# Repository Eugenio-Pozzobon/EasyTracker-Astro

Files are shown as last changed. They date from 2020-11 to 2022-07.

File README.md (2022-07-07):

# Desenvolvimento de uma Plataforma Equatorial de Baixo Custo para Astrofotografia

Este repositório armazena os arquivos desenvolvidos durante o Trabalho de Conclusão de Curso do Aluno Eugênio Pozzobon, sob orientação do professor Rafael Beltrame.
O TCC pode ser obtido neste link: https://repositorio.ufsm.br/handle/1/25238

## Aplicativo Android
* Os arquivos do  _software_ Android, que opera junto com a eletrônica arquivada neste repositório, pode ser encontrado [neste link.](https://github.com/Eugenio-Pozzobon/EasyTracker-Android-App)
* Para apenas instalar, acesse [este link para a Google Play](https://play.google.com/store/apps/details?id=com.epp.com.easytracker) 

## Licença
Os arquivos de documentação estão licenciados sob Creative Commons CC BY-SA. Dessa forma, são livre para redistribuição. Códigos do Hardware Embarcado estão licenciados sob GPLV3, implicando que os autores devem ser permanentemente creditados por esses arquivos. Os arquivos de desenvolvimento CAD são livres.

### Como contribuir?
Antes de qualquer coisa, leia e estude a documentação do TCC. Após isso, envie um email para eugenio.pozzobon@acad.ufsm.br para saber como ajudar no projeto.

---

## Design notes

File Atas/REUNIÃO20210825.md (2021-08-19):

### Algoritmo de calibração de bússola de um DJI (?)

* Auto detecta erro de calibração
	* Verifica quando as constantes de calibração (valores mínimos e máximos de medição não estão conferindo com a realidade)
* Auto detecta calibração concluída
	* Giroscópio

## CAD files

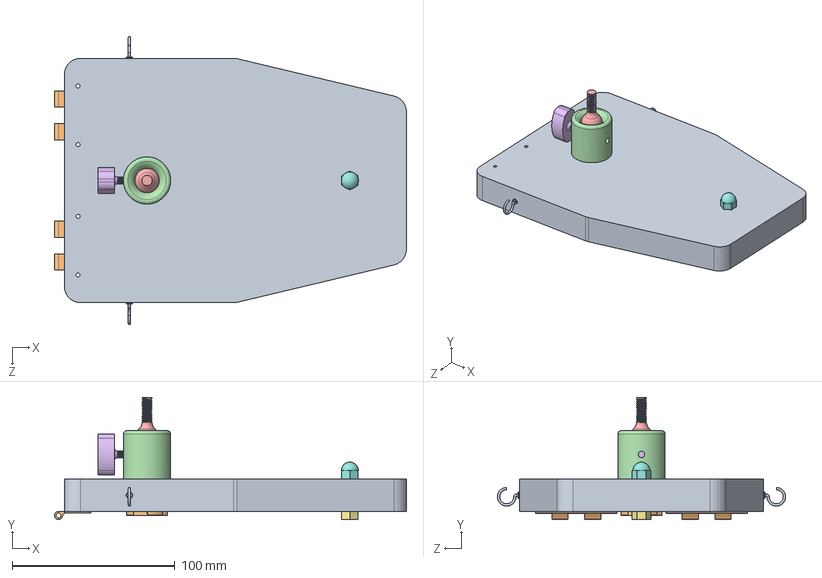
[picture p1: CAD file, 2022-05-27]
CAD/Base Superior/BDT_S_A_17_v01.SLDASM
216.0 x 75.0 x 176.9 mm
BDT_S_P_13_v01
BDT_S_P_15_v01 x 2
BDT_G_P_22_v01
BDT_S_P_18_v01
BDT_S_P_19_v01
BDT_S_P_20_v01
BDT_G_F_25_v01
BDT_G_F_26_v01
BDT_G_F_24_v01 x 2
TNUT-3-8

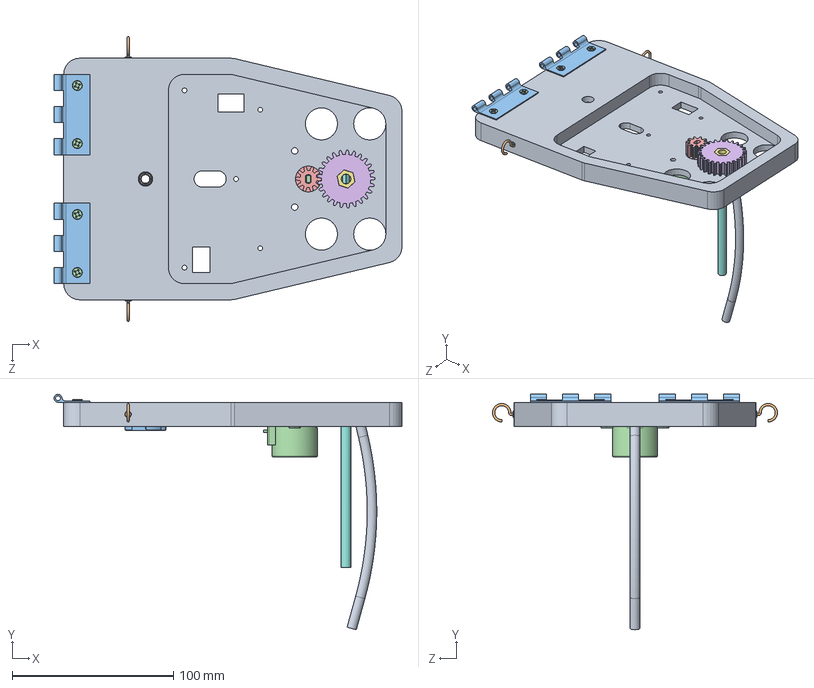
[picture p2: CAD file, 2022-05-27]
CAD/Base Inferior/BDT_I_A_16_v01.SLDASM
216.0 x 146.2 x 176.9 mm
BDT_I_P_11_v01
BDT_I_P_12_v01 x 2
BDT_E_P_01_v01
BDT_I_P_06_v01
BDT_I_P_07_v01
BDT_G_F_26_v01
Gambi^BDT_I_A_16_v01
BDT_G_F_05_v01
BDT_G_F_24_v01 x 2
flat countersunk head tapping screw_am x 4
INSERTO

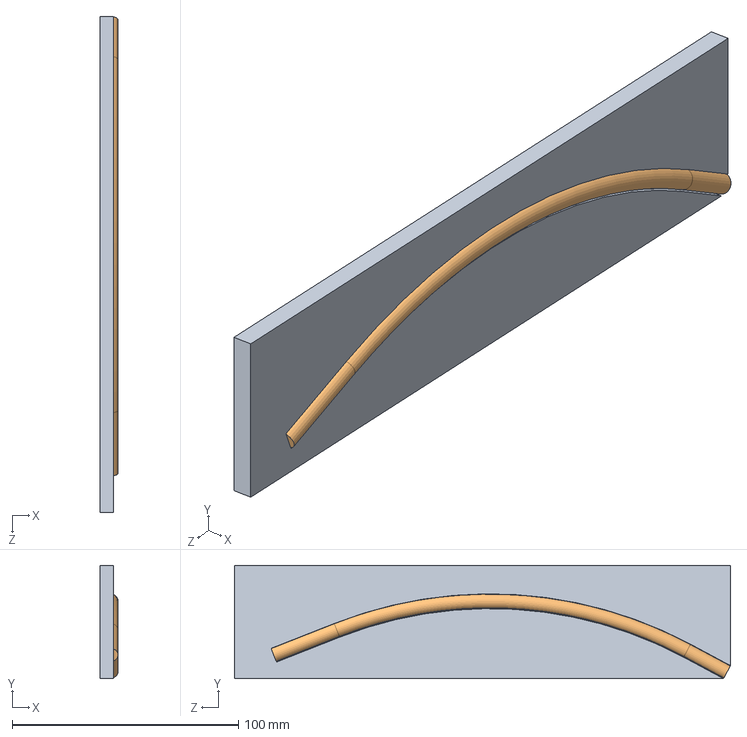
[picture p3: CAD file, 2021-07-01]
CAD/Fabricação/Montagem Gabarito.SLDASM
8.00 x 50.0 x 219.0 mm
Gabarito Eixo Curvo
BDT_G_F_05_v01

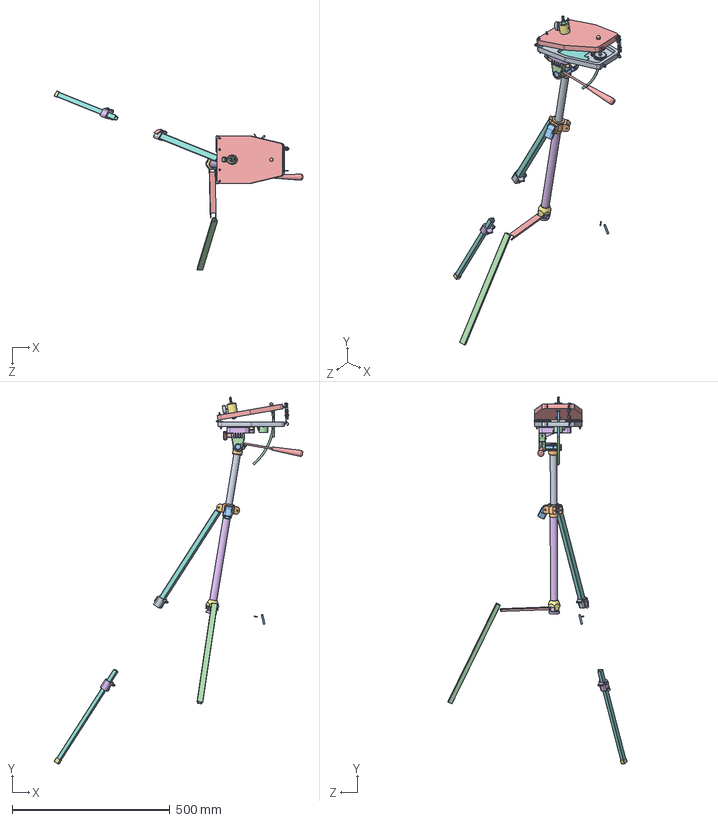
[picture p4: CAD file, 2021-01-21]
CAD/BDT_GLOBAL_ASSEMBLY.SLDASM
787.4 x 1162.0 x 567.4 mm
BDT_I_P_11_v01
BDT_G_P_22_v01 x 2
BDT_I_P_12_v01 x 2
Step - 28BYJ-48
hex nut style 1_am x 8
flat head screw_am x 8
BDT_G_F_24_v01 x 4
BDT_I_P_06_v01
BDT_I_P_07_v01
PORCAM6tTRAVA x 2
BDT_G_F_05_v01
BDT_S_P_13_v01
BDT_S_P_15_v01 x 2
BDT_S_P_18_v01
BDT_S_P_19_v01
BDT_S_P_20_v01
socket button head cap screw_ai
PORCAM6
BDT_G_P_14_v01 x 2
BDT_G_F_10_v01 x 2
PCBfake^BDT_GLOBAL_ASSEMBLY

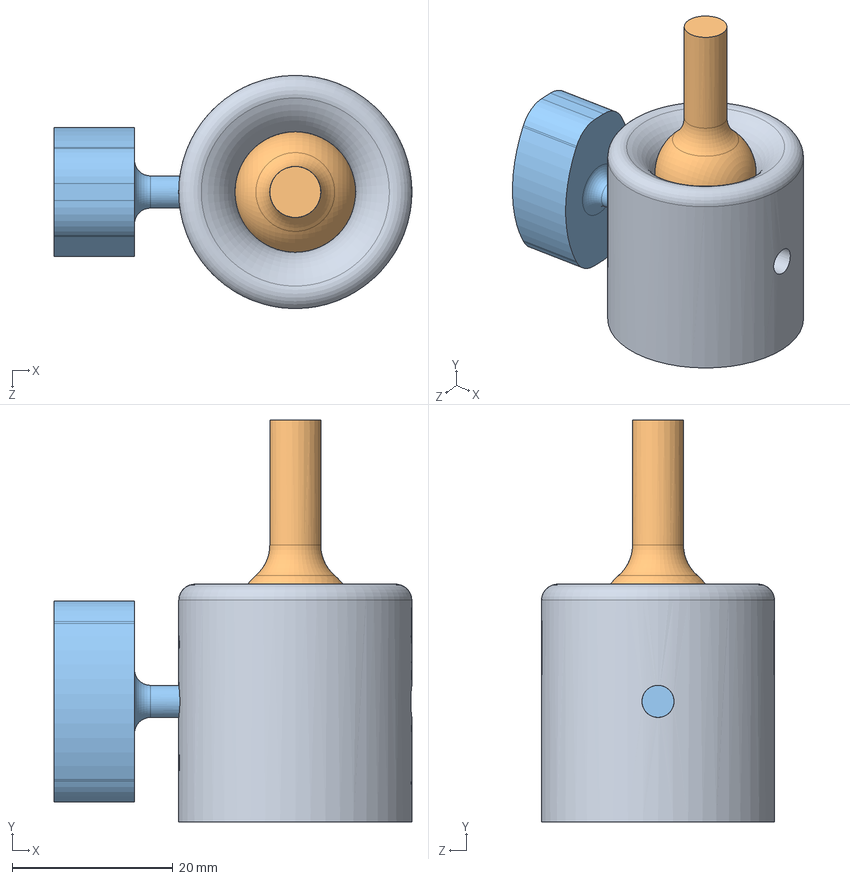
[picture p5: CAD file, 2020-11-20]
CAD/Base Superior/Cabeça de Tripé/BDT_S_A_21_v01.SLDASM
44.5 x 50.0 x 29.0 mm
BDT_S_P_18_v01
BDT_S_P_19_v01
BDT_S_P_20_v01

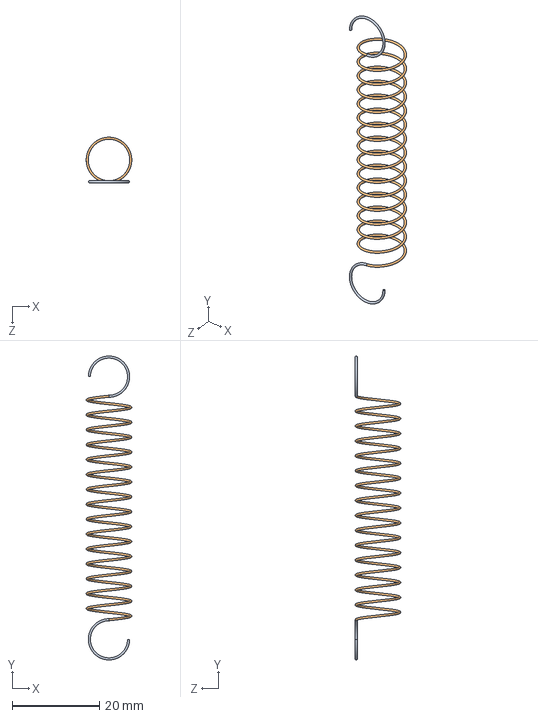
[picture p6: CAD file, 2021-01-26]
CAD/Fixadores/Mola de Tração.sldasm
10.5 x 69.9 x 10.5 mm
BDT_G_F_10_v01 x 2
BDT_G_F_09_v01

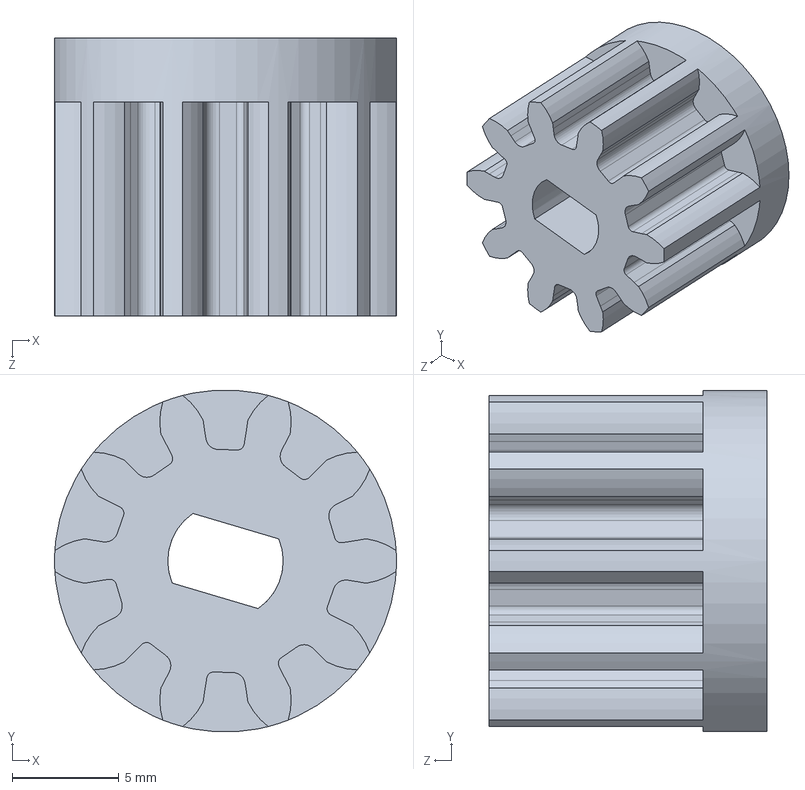
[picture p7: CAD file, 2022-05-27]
CAD/Base Inferior/BDT_I_P_06_v01.sldprt
16.0 x 16.0 x 13.0 mm

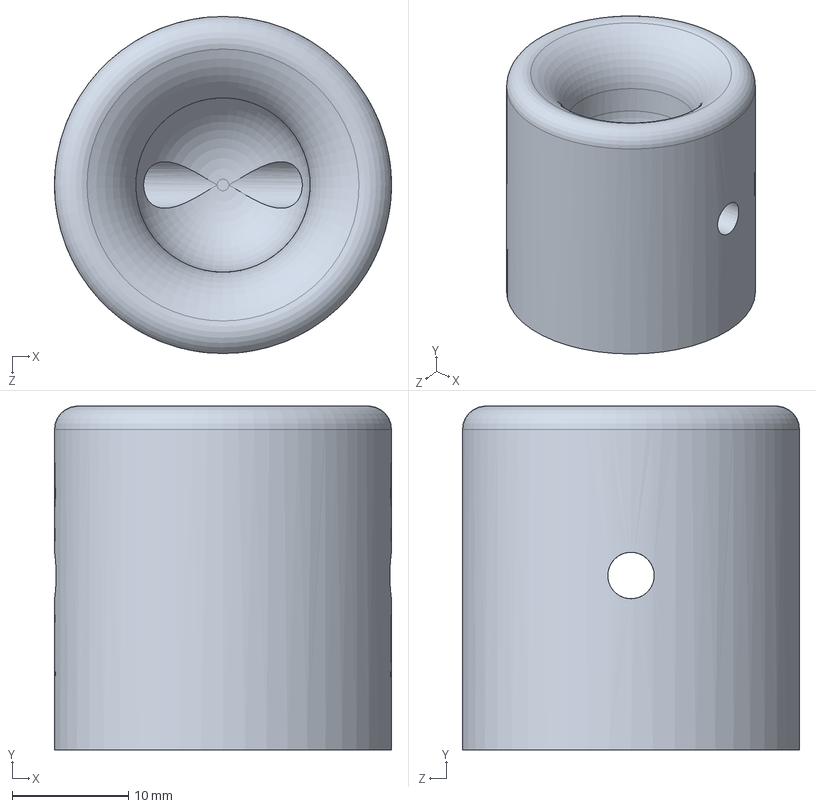
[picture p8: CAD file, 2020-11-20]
CAD/Base Superior/Cabeça de Tripé/BDT_S_P_18_v01.SLDPRT
29.0 x 29.6 x 29.0 mm

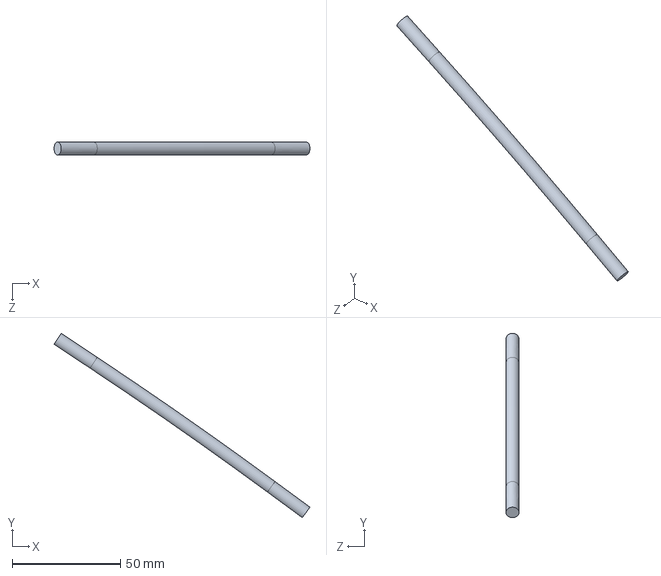
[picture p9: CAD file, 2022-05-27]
CAD/BDT_G_F_05_v01.sldprt
118.2 x 85.1 x 6.00 mm

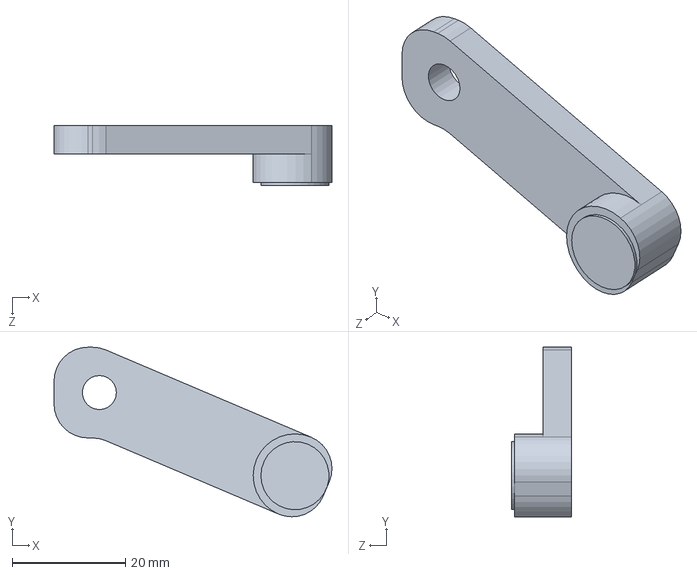
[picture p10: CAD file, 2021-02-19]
CAD/Eletrônica/BDT_E_P_03_v01.SLDPRT
49.0 x 29.9 x 10.5 mm

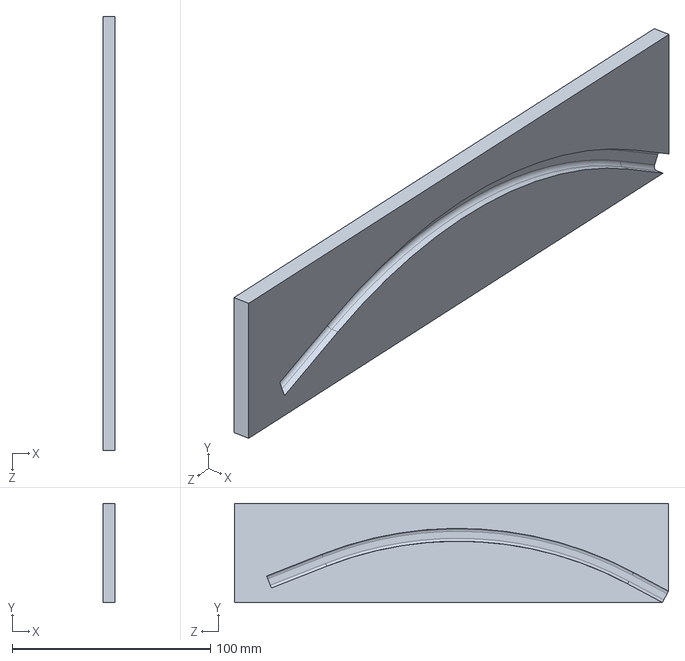
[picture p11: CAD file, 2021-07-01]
CAD/Fabricação/Gabarito Eixo Curvo.SLDPRT
6.00 x 50.0 x 219.0 mm

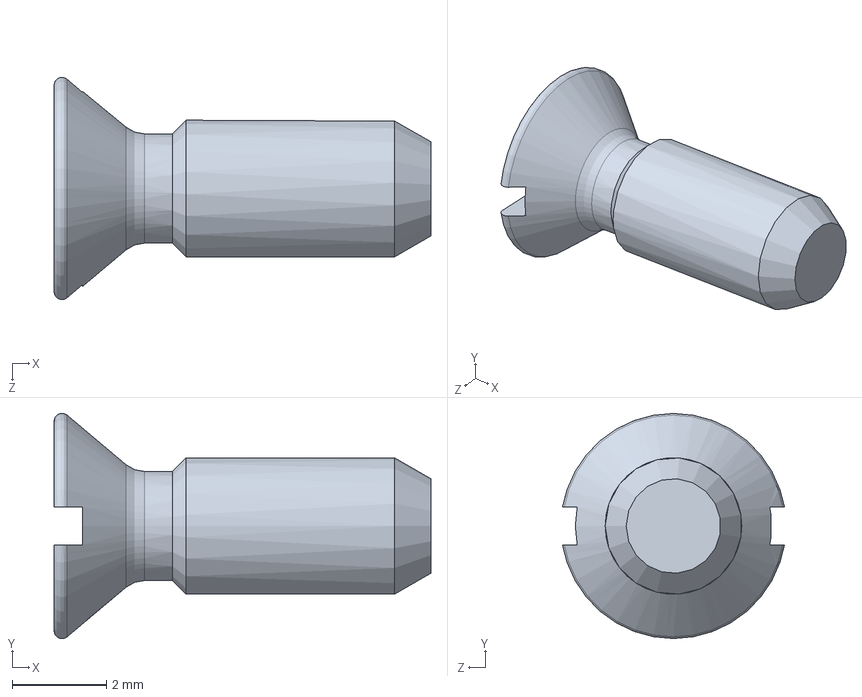
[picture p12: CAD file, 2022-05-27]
CAD/Fixadores/a.SLDPRT
8.00 x 4.78 x 4.72 mm

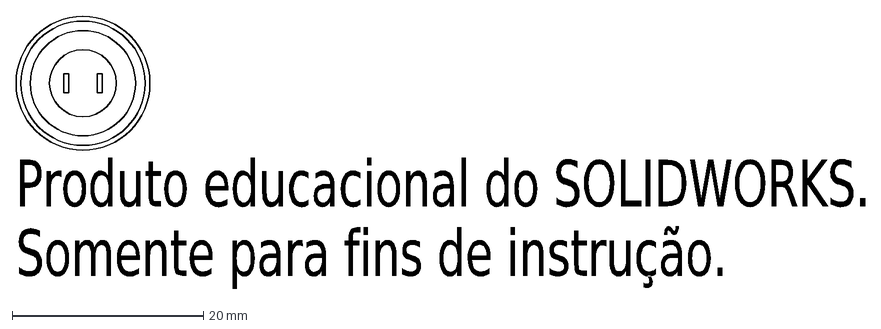
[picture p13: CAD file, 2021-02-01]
Electronics/button.DXF
Produto educacional do SOLIDWORKS.
Somente para fins de instrução.

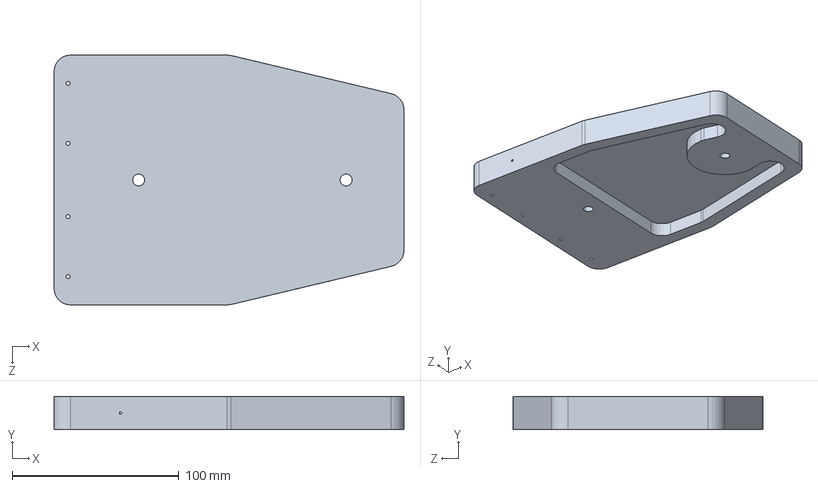
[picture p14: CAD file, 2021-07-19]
CAD/Base Superior/BDT_S_P_13_v01.SLDPRT
210.0 x 20.0 x 150.0 mm

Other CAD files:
CAD/Base Superior/Cabeça de Tripé/BDT_S_P_19_v01.SLDPRT
CAD/BDT_G_P_14_v01.sldprt
CAD/Eletrônica/BDT_E_P_27_v01.SLDPRT
CAD/Fixadores/TNUT-3-8.SLDPRT
CAD/Base Inferior/BDT_I_P_07_v01.SLDDRW
CAD/Base Inferior/BDT_I_P_07_v01.sldprt
CAD/Base Inferior/BDT_I_P_11_v01.DXF
CAD/Base Inferior/BDT_I_P_11_v01.SLDPRT
CAD/Base Inferior/BDT_I_P_12_v01.SLDPRT
CAD/Base Inferior/INSERTO.SLDPRT
CAD/Base Superior/BDT_S_P_15_v01.SLDPRT
CAD/Base Superior/Cabeça de Tripé/BDT_S_P_20_v01.SLDPRT
CAD/Eletrônica/BDT_E_P_01_v01.SLDPRT
CAD/Eletrônica/BDT_E_P_02_v01.SLDPRT
CAD/Eletrônica/BDT_E_P_28_v01.SLDPRT
CAD/Eletrônica/BDT_E_P_29_v01.SLDPRT
CAD/Eletrônica/Peça1.SLDPRT
CAD/Eletrônica/startbutton.SLDPRT
CAD/Fabricação/BDT_E_P_03_v01.DWG
CAD/Fabricação/BDT_G_F_05_v01.SLDDRW
CAD/Fabricação/BDT_I_P_06_v01.STEP
CAD/Fabricação/BDT_I_P_07_v01.STEP
CAD/Fabricação/BDT_I_P_11_v01.DWG
CAD/Fabricação/BDT_I_P_11_v01.SLDDRW
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

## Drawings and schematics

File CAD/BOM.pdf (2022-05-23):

# BILL OF MATERIALS (BOM)

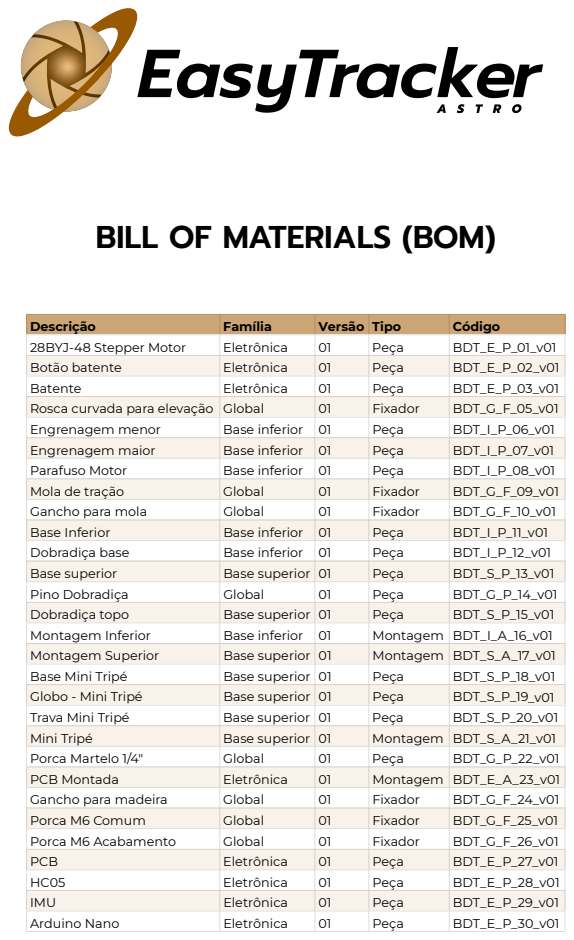
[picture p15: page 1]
Descrição; Família; Versão Tipo; Código; 28BYJ-48 Stepper Motor; Eletrônica; Peça; BDT_E_P_01_v01; Botão batente; BDT_E_P_02_v01; Batente; BDT_E_P_03_v01; Rosca curvada para elevação Global; Fixador; BDT_G_F_05_v01; Engrenagem menor; Base inferior 01; BDT_I_P_06_v01; Engrenagem maior; BDT_I_P_07_v01; Parafuso Motor; BDT_I_P_08_v01; Mola de tração; Global; BDT_G_F_09_v01; Gancho para mola; BDT_G_F_10_v01; Base Inferior; BDT_I_P_11_v01; Dobradiça base; BDT_I_P_12_v01; Base superior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

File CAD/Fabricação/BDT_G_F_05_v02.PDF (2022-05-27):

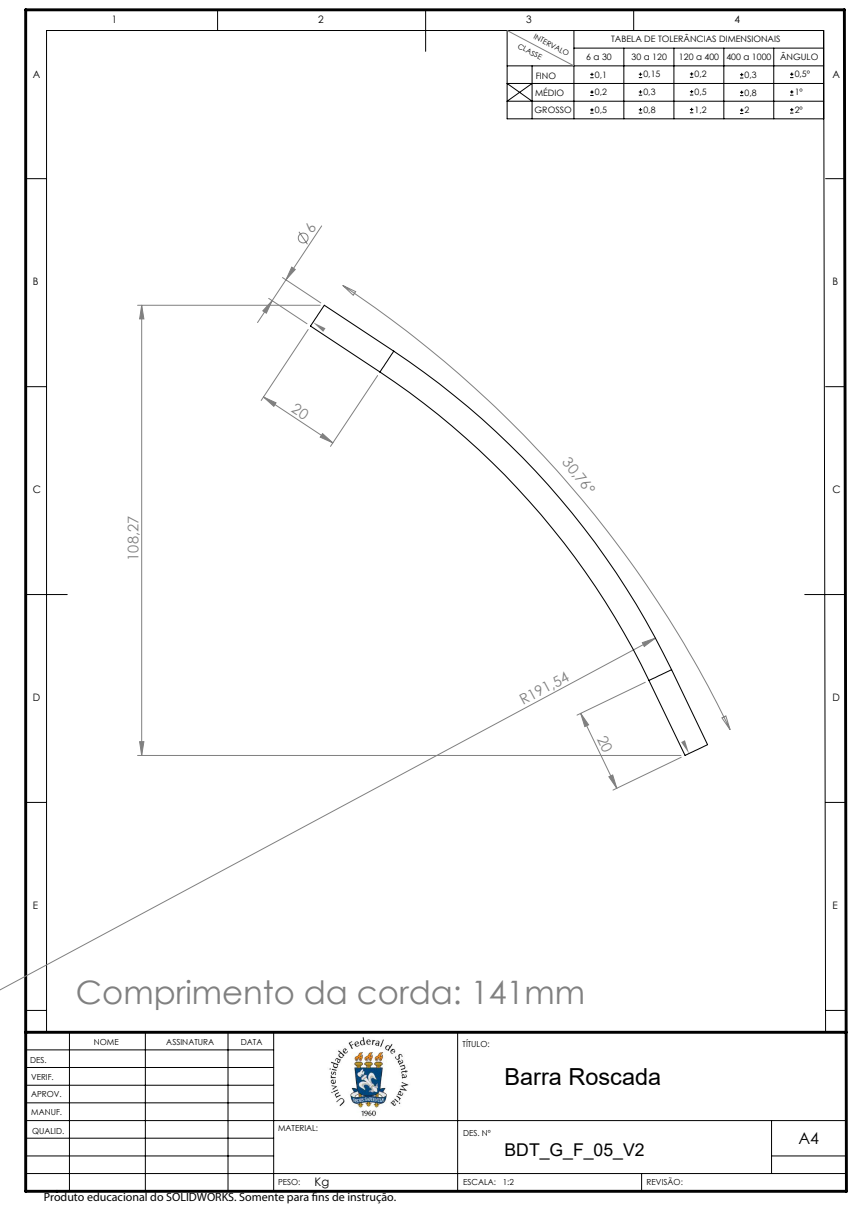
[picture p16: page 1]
ÂNGULO; TABELA DE TOLERÂNCIAS DIMENSIONAIS; ESCALA: 1:2; DES. Nº; Barra Roscada

Comprimento da corda: 141mm

Produto educacional do SOLIDWORKS. Somente para ns de instrução.

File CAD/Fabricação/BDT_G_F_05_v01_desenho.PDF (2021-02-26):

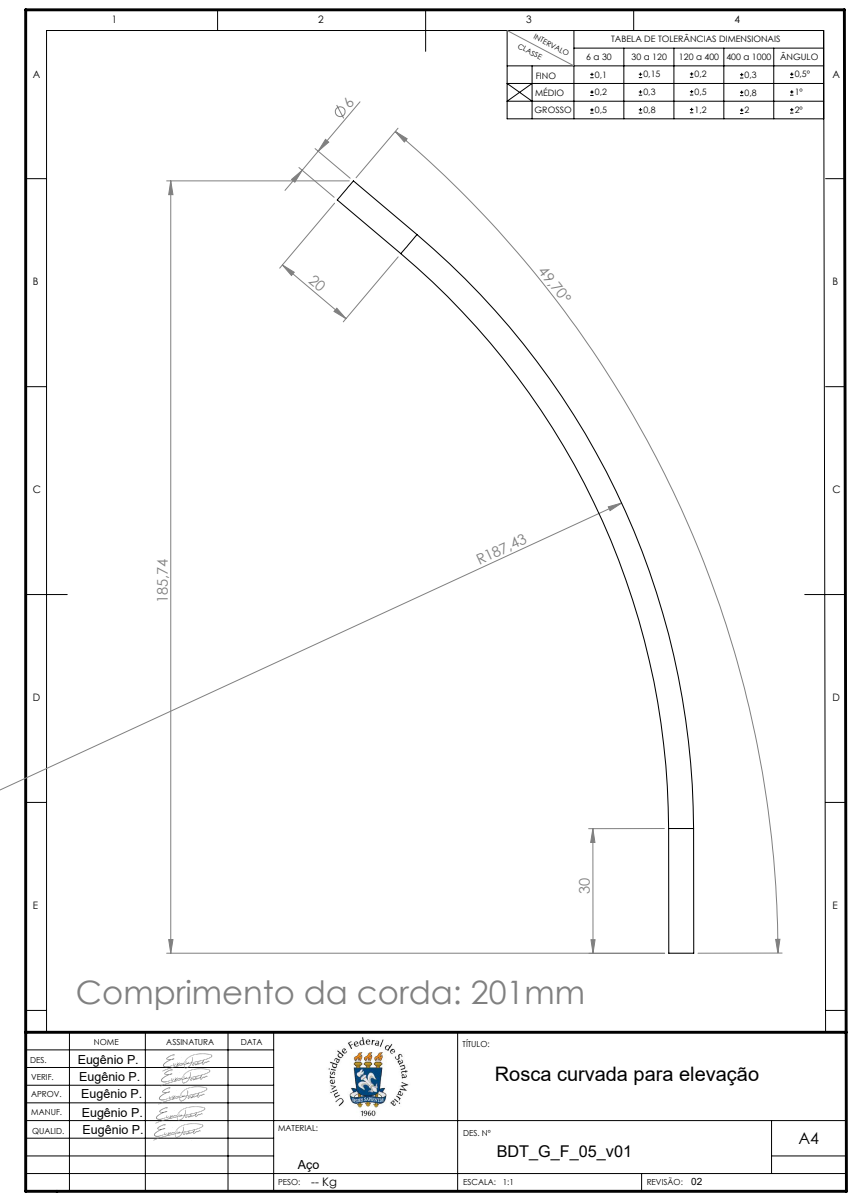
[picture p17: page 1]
ÂNGULO; TABELA DE TOLERÂNCIAS DIMENSIONAIS; ESCALA: 1:1; DES. Nº; REVISÃO:; Eugênio P. Eugênio P. Eugênio P.; Eugênio P.

Comprimento da corda: 201mm

TÍTULO:
Rosca curvada para elevação

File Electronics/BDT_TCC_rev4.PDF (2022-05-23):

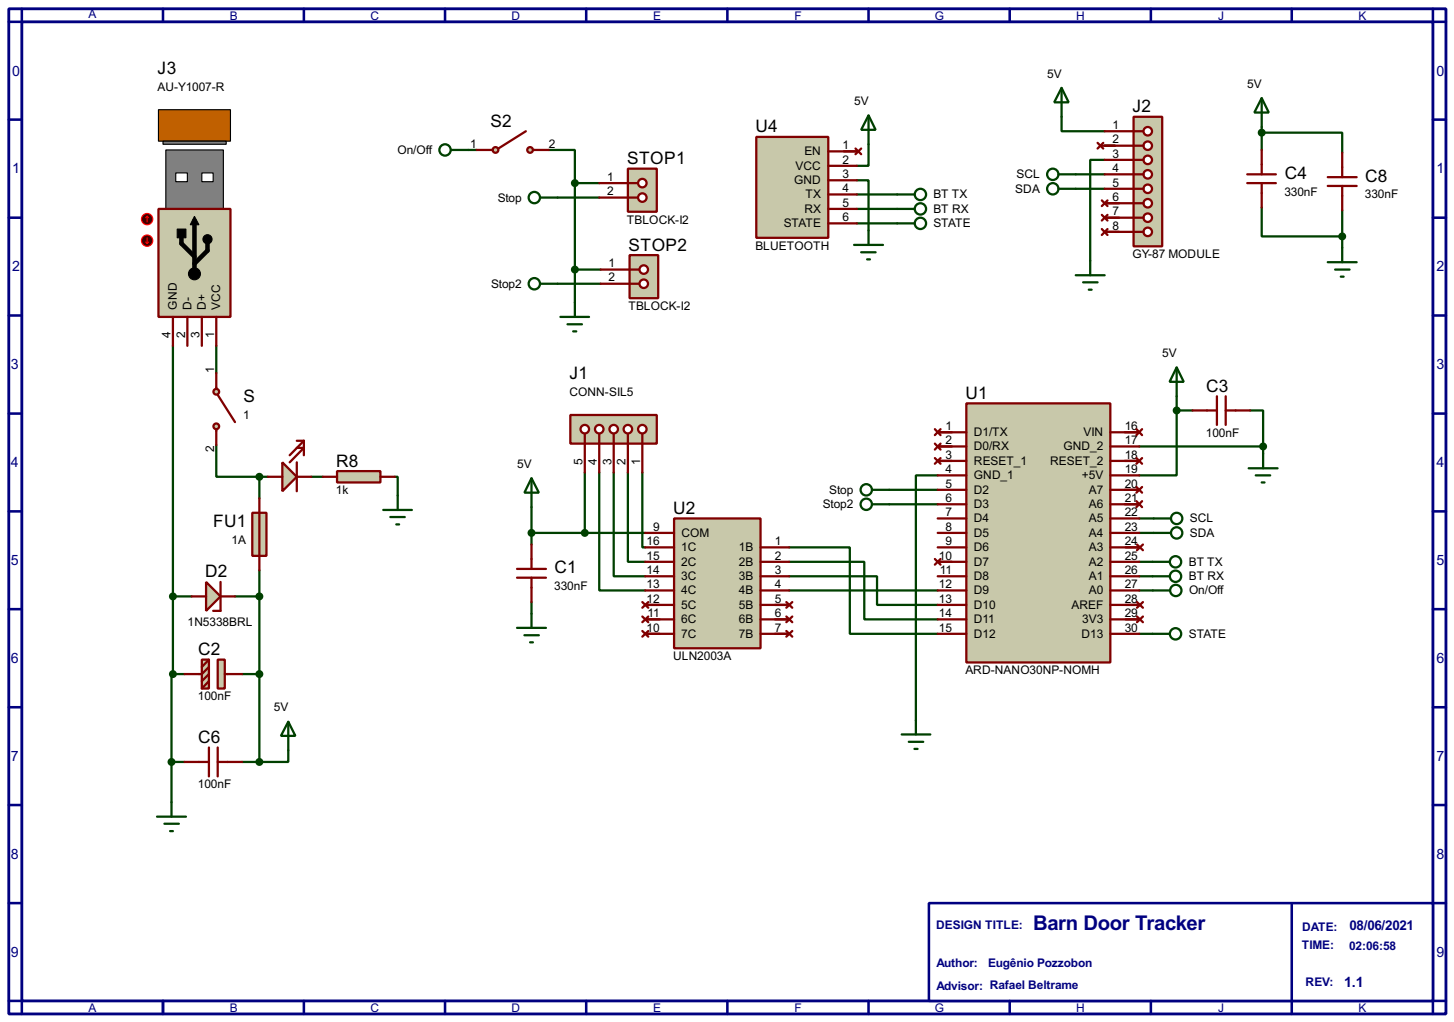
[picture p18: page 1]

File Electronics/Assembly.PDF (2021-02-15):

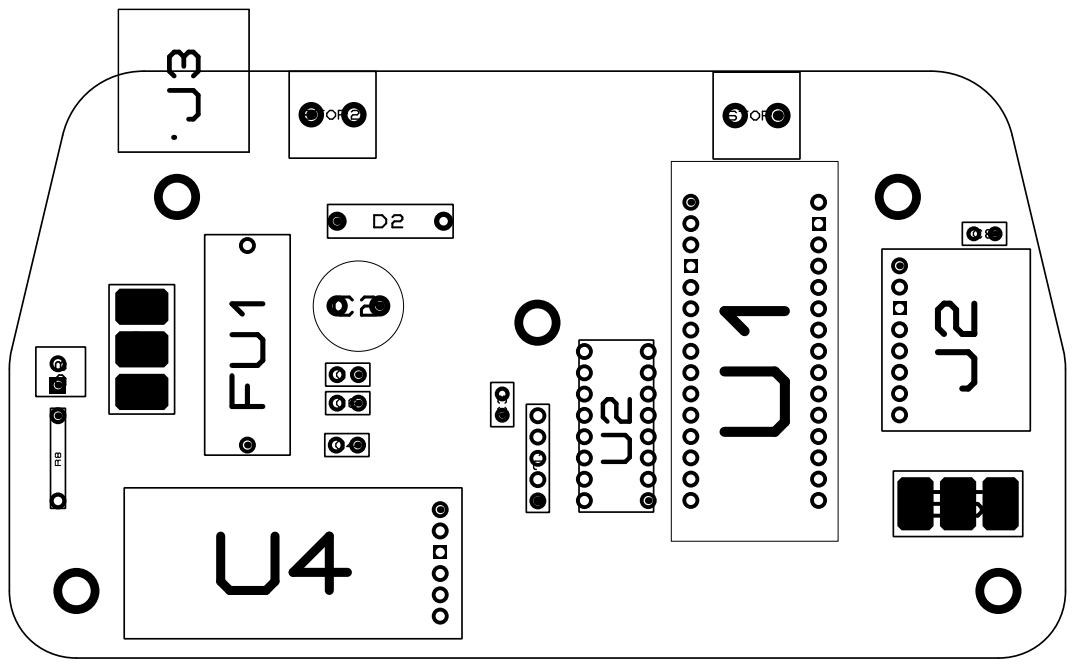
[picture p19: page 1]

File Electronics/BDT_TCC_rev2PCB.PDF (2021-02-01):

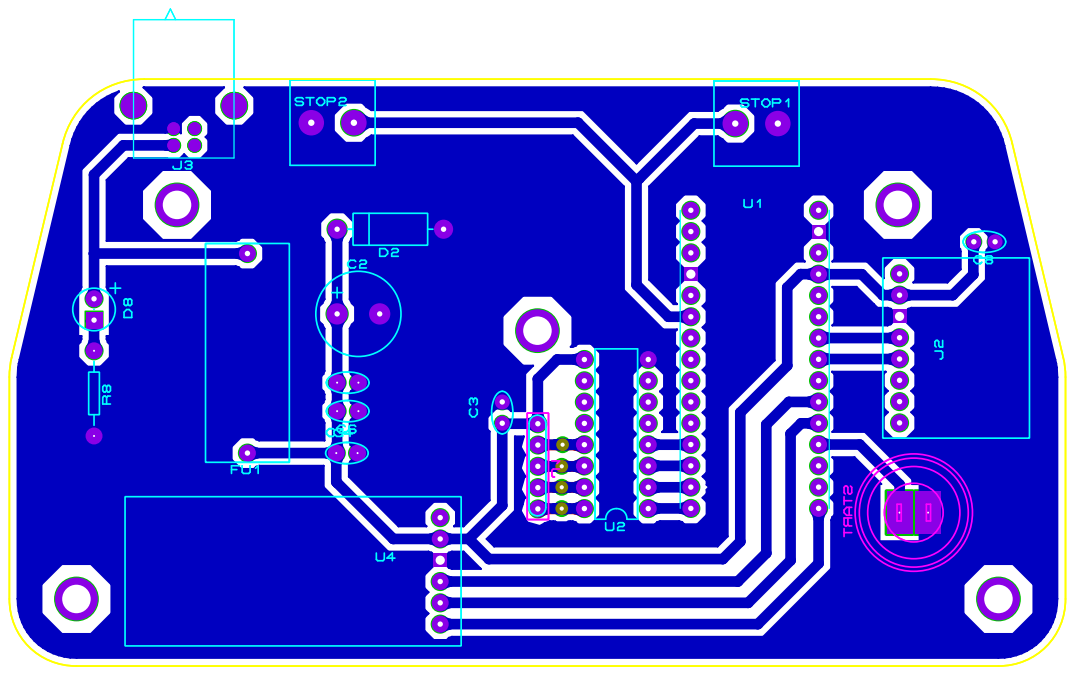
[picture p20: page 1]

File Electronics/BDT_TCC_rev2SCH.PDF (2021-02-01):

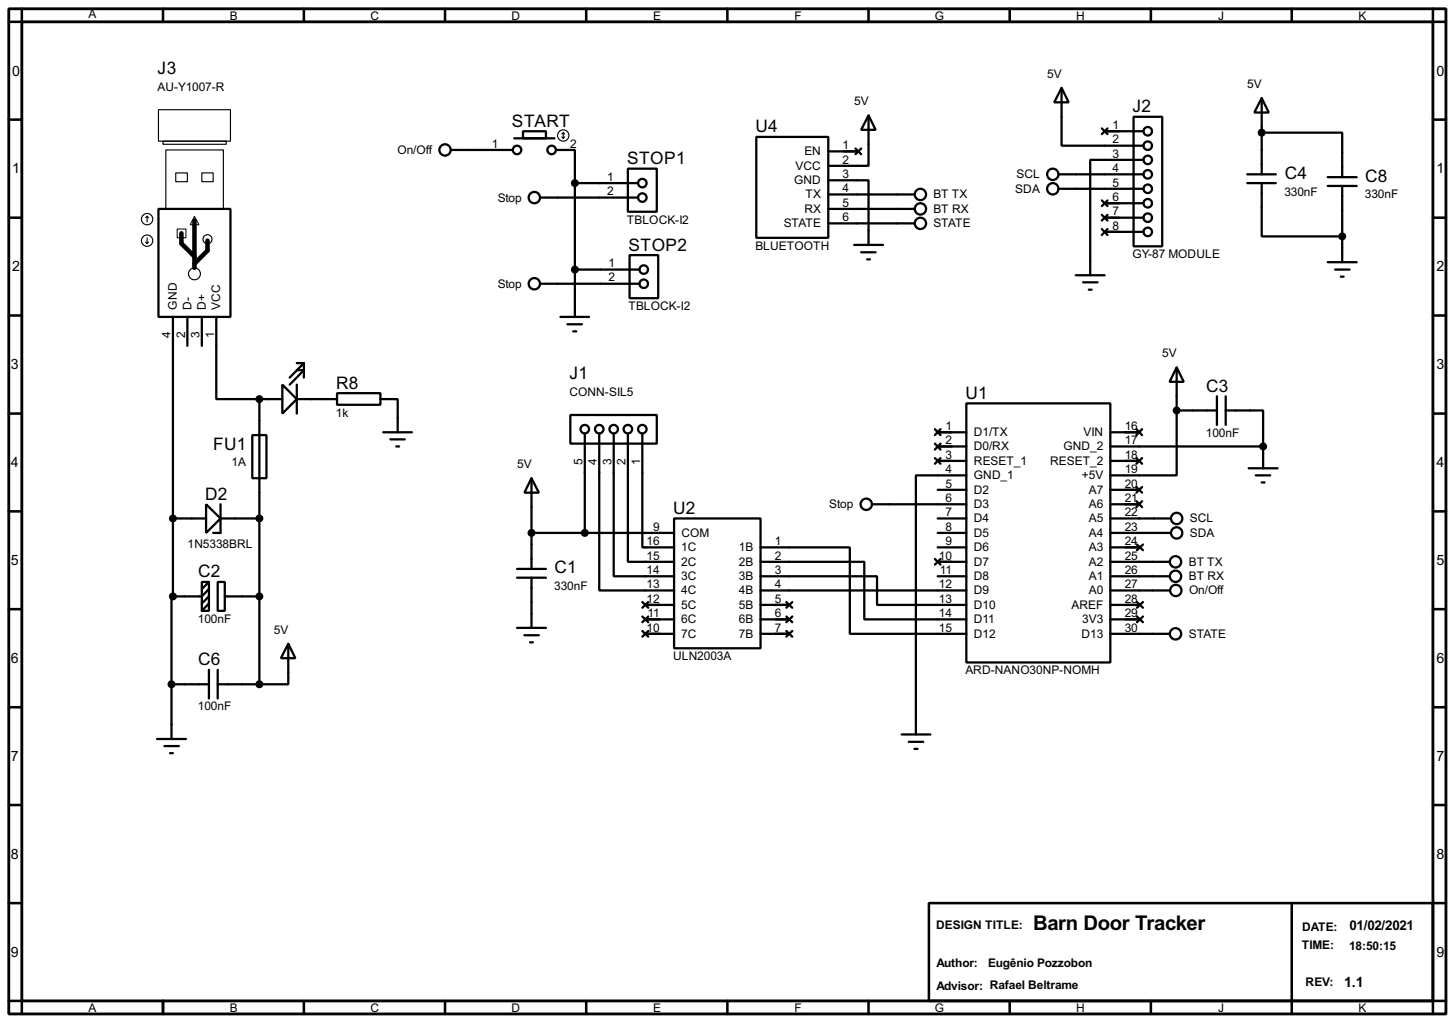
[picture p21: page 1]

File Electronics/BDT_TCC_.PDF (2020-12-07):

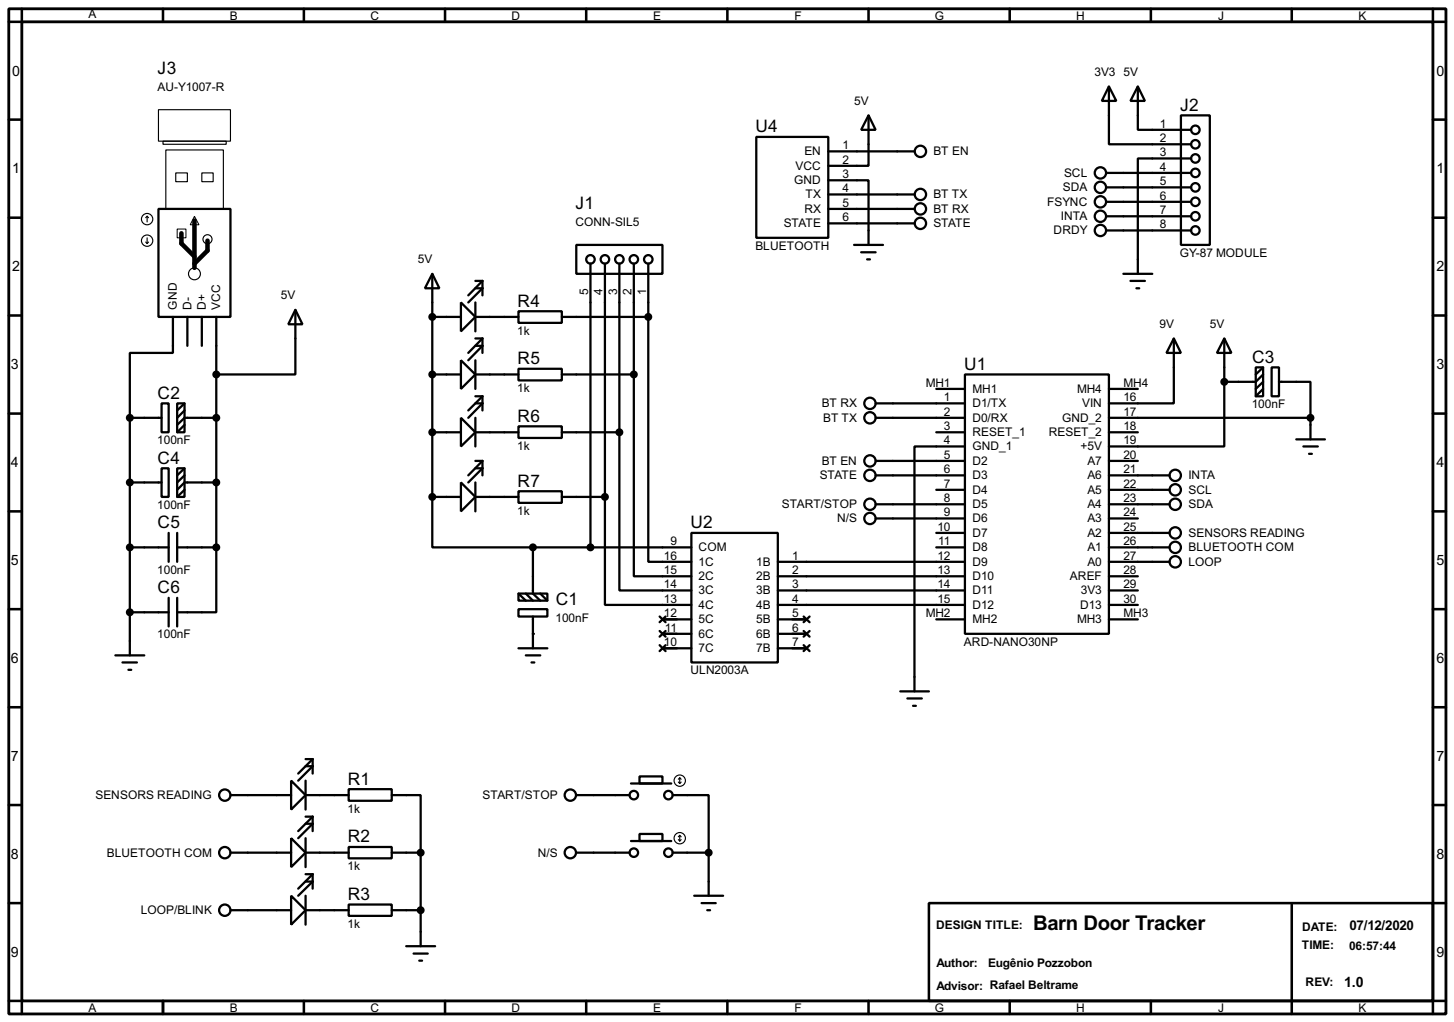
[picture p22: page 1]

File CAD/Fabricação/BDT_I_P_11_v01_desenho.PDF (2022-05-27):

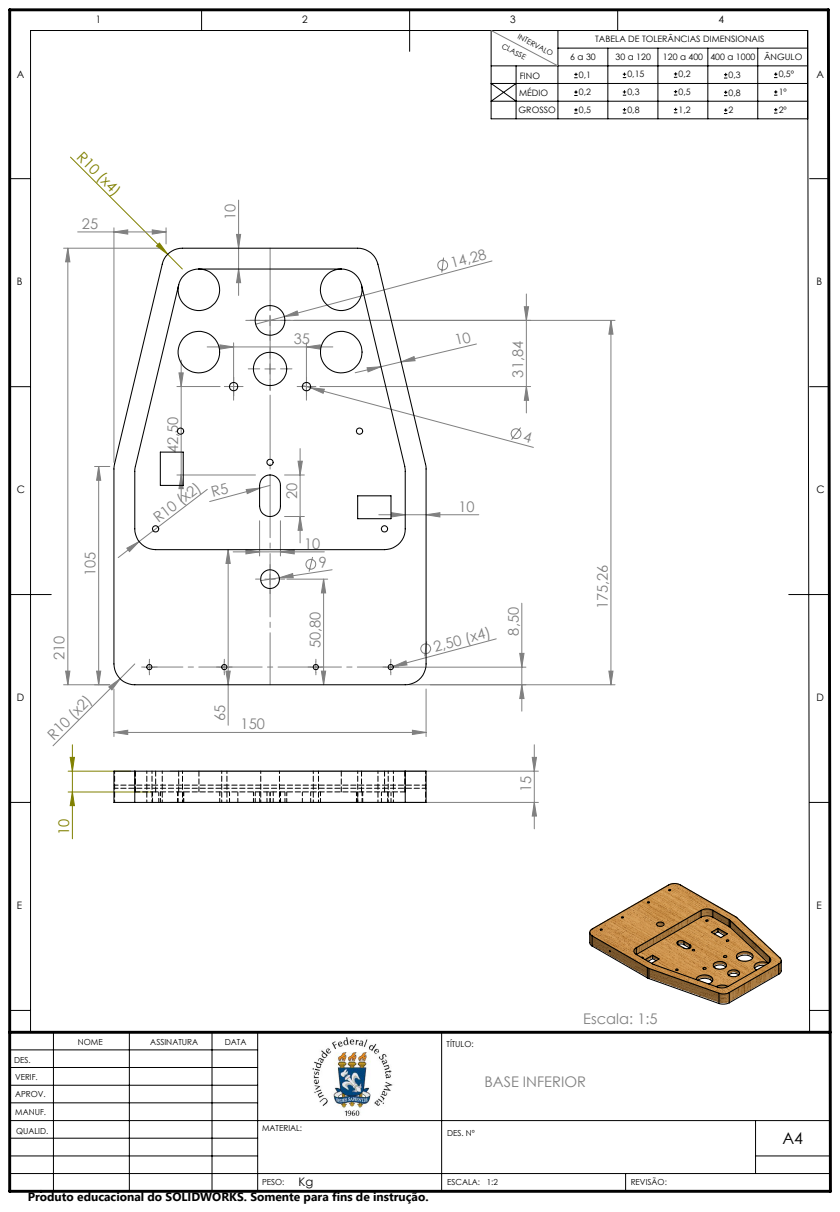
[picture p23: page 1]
ÂNGULO; TABELA DE TOLERÂNCIAS DIMENSIONAIS; Escala: 1:5; BASE INFERIOR; ESCALA: 1:2; DES. Nº

Produto educacional do SOLIDWORKS. Somente para fins de instrução.

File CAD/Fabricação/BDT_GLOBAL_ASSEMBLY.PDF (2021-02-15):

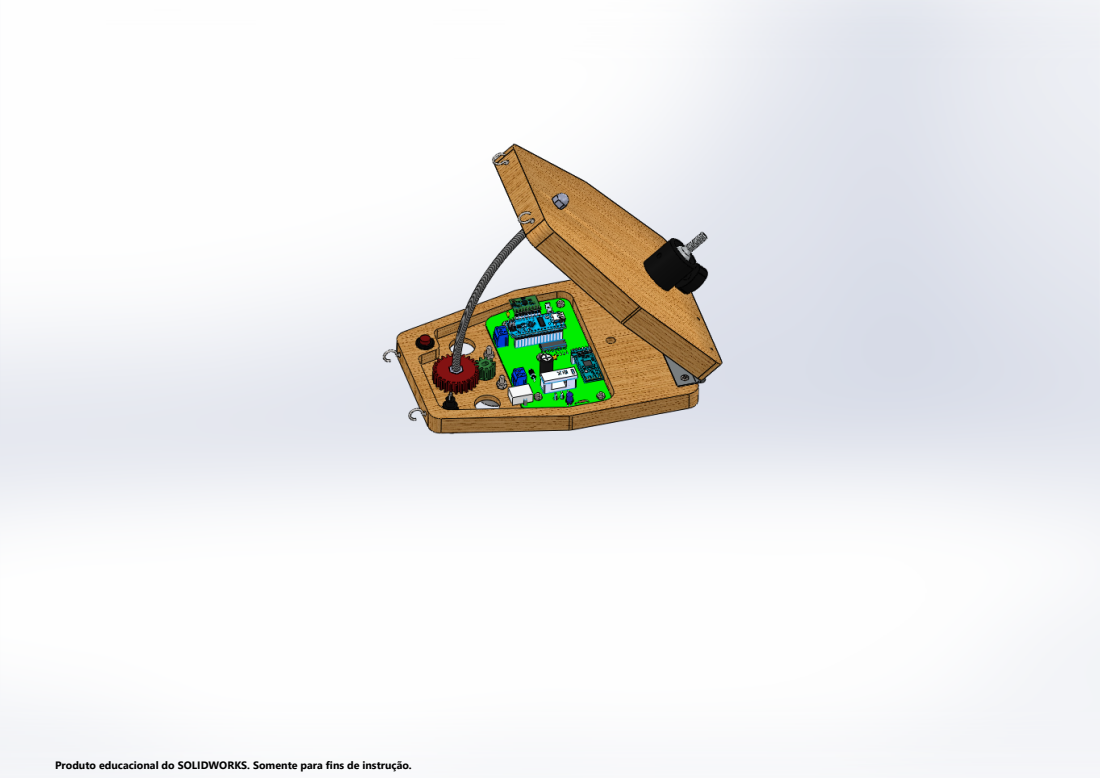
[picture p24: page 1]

Produto educacional do SOLIDWORKS. Somente para fins de instrução.

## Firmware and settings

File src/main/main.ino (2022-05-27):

/*
main.ino - main file of EasyTracker Astro System

Version: 1.0.0
Copyright (C) 2022  Eugênio Pozzobon

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
You should have received a copy of the GNU General Public License
along with this program.  If not, see <http://www.gnu.org/licenses/>.
*/

#include "configuration.h"

// Librarys includes
#include "Wire.h"
#include "MPU6050_bdt.h"
#include "HMC5883L_bdt.h"
#include "stp.h"
//#include <Stepper.h>

#include <SoftwareSerial.h>
#include <EEPROM.h>
#include <avr/wdt.h>

// Bluetooth variables
SoftwareSerial bluetoothSerial(16, 15); // RX/TX
unsigned long timerBluetoothRestartMessages = 0;
unsigned long timerBluetoothRecieveMessages = 0;
unsigned long timerBluetoothSendMessages = 0;
const byte bluetoothStatePin = 13;

//User Input Variables
char availableUserOption = '0';
bool manualDeactivation = true, remoteDeactivation = false;
bool manualActivation = false, lastManualActivation = false;
bool remoteActivation = false;

// Acelerometer variables
MPU6050 accelgyro;
float angleX, angleY, angleZ;
unsigned long gyroIntegrateTimer = 0; //Timer to interate Gyroscope axis and get Gyro part of Pitch and Roll angle.
const float accelGyroRelation = 0.5; //How mucth Gyro and Accel is consider for interate Pitch and Roll. 0 means that only accel will be used.

// Magnetometer variables
HMC5883L mag;
int mx, my, mz;
float mxCalibrated, myCalibrated, mzCalibrated;

// Calibration factors
int mxMin = EEPROM.read(0) << 8 | EEPROM.read(1);
int myMin = EEPROM.read(2) << 8 | EEPROM.read(3);
int mzMin = EEPROM.read(4) << 8 | EEPROM.read(5);
int mxMax = EEPROM.read(6) << 8 | EEPROM.read(7);
int myMax = EEPROM.read(8) << 8 | EEPROM.read(9);
int mzMax = EEPROM.read(10) << 8 | EEPROM.read(11);

// Calculation variables
const byte mediaMovelArray = 8;
float compassAngle = 0;
float reads[mediaMovelArray];

// Timer variables
unsigned long timerMpuData, timerStepperMicros = 0, timerLoop = 0;

// Stepper variables
boolean stepperState = false;
const int startButtonPin = 14;
const int stopButtonPin = 2;
const int stopButtonPin_sec = 3;
const int stepsPerRevolution = 4096 / 2;
HalfStepper myStepper = HalfStepper(stepsPerRevolution, 12, 10, 11, 9);

void setup() {
  //Initializate Whatchdog
  wdt_enable(WDTO_8S);

  // Initializate Variables
  for (int i = 0; i < mediaMovelArray; i++) {
    reads[i] = 0;
  }

  // Initializate Serial
#ifdef DEBUG
  Serial.begin(115200);
  printCalibrationInfo();
#endif

  // Initializate Bluetooth
  bluetoothSart();

  // Initializate I2C Bus
  beginI2cBus();
  initializeDevicesI2c();

  // Initializate Arduino pins
  //  pinMode(ledPin, OUTPUT);
  pinMode(startButtonPin, INPUT_PULLUP);
  pinMode(stopButtonPin, INPUT_PULLUP);
  pinMode(stopButtonPin_sec, INPUT_PULLUP);

  // Setup Stepper
  myStepper.setSpeed(STP_SPEED);
}

void loop() {

  wdt_reset();

  stepperState = checkStepperCondition();
  if (stepperState == true) {
    myStepper.step(runningSteps); //runs Stepper motor and elevate the plataform
    if (bluetoothSerial.available() > 0) {
      if (manualActivation && !remoteActivation) {
        bluetoothSerial.print("s,s\n");
      }
      availableUserOption = bluetoothSerial.read(); //flush buffer
    }
  } else {
    if (bluetoothSerial.available() > 0) {
      if (remoteActivation) {
        bluetoothSerial.print("n,n\n");
        remoteActivation = false;
      }
    }
  }

  if (stepperState == false) {
    getData();
    serialCommunication();
    bluetoothCommunication();
  }

  manageUserOption();

#ifdef DEBUG
//  Serial.print("manualActivation "); Serial.println(manualActivation);
//  Serial.print("manualDeactivation "); Serial.println(manualDeactivation);
//  Serial.print("remoteActivation "); Serial.println(remoteActivation);
//  Serial.print("remoteDeactivation "); Serial.println(remoteDeactivation); Serial.println();
#endif
}


bool checkStepperCondition() {
  int nullvar = analogRead(startButtonPin); //não tem função nenhuma, não serve pra nada, porém o código só funciona se estiver aqui!
  if (millis() > 5000) {// dont get the starting set of pullup as a true value
    if (!manualActivation && !digitalRead(startButtonPin)) {
      manualActivation = true;
      manualDeactivation = false;
      remoteDeactivation = false;
    }
    if (manualActivation && digitalRead(startButtonPin)) {
      manualActivation = false;
      manualDeactivation = true;
      remoteActivation = false;
    }
  }
  bool stopState = false;//(!digitalRead(stopButtonPin) || !digitalRead(stopButtonPin_sec));
  if(stopState){
    manualActivation = false;
    remoteActivation = false;
  }
  return ((manualActivation || remoteActivation) && (!manualDeactivation && !remoteDeactivation && !stopState));
}

bool checkBluetoothCondition() {
  return (!digitalRead(bluetoothStatePin));
}

void serialCommunication() {
#ifdef DEBUG
  while (Serial.available() > 0) {
    availableUserOption = Serial.read();
  }
#endif
}


/*
   @brief
   @note
   @param
   @return
*/
void manageUserOption() {
  if (availableUserOption == 'c') {
    compassCalibration();
  }
  if (availableUserOption == 's') {
    remoteActivation = true;
    remoteDeactivation = false;
    manualDeactivation = false;
    bluetoothSerial.print("s,s\n"); //while writebuffer isnt clean in android, send the buffer that trigger an internal clean
  }
  if (availableUserOption == 'n') {
    remoteDeactivation = true;
    remoteActivation = false;
    bluetoothSerial.print("n,n\n"); //while writebuffer isnt clean in android, send the buffer that trigger an internal clean
  }
  if (availableUserOption == 'r') {
    ressetCalibration();
  }
  if (availableUserOption == '1') {
    remoteActivation = true;
    remoteDeactivation = false;
  }
  availableUserOption = '0';
}

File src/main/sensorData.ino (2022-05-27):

/*
sensorData.ino - file that process sensor data at EasyTracker

Version: 1.0.0
Copyright (C) 2022  Eugênio Pozzobon

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
You should have received a copy of the GNU General Public License
along with this program.  If not, see <http://www.gnu.org/licenses/>.
*/

void getData() {
  if (((millis() - timerMpuData) >= 0) && !stepperState) {

    timerMpuData = millis();
    //1ms to get all data with 400kHz and 5ms with 100kHz
    accelgyro.readNormalizeAccel();
    accelgyro.readNormalizeGyro();

    mag.getHeading(&mx, &my, &mz);


    angleCalculation();
    //compassCalculation();

    debugSensor();
  }
}

void angleCalculation() { //900us usando int_16t e 1300us usando float
  unsigned long cT = micros(); // contar tempo de loop
  unsigned long dT = cT - gyroIntegrateTimer; //Variable for measure angle with gps and make integration of values
  gyroIntegrateTimer = cT;

  // Gyro Calculations convert gyro raw to degrees per second
  //  rate_gyr_x = accelgyro.ngx;
  //  rate_gyr_y = accelgyro.ngy;
  //  rate_gyr_z = accelgyro.ngz;
  //  gyroXangle += rate_gyr_x * dT;
  //  gyroYangle += rate_gyr_y * dT;
  //  gyroZangle += rate_gyr_z * dT;

  // Roll angle
  angleX = accelGyroRelation * (-angleX + accelgyro.ngx * (float(dT) / 1000000)) + (1 - accelGyroRelation) *
           (atan2(accelgyro.nax, sqrt(pow(accelgyro.nay, 2) + pow(accelgyro.naz, 2))) * 180) / 3.14;
  angleX = - angleX;

  // Pitch angle
  angleY = accelGyroRelation * (-angleY + accelgyro.ngy * (float(dT) / 1000000)) + (1 - accelGyroRelation) *
           (atan2(accelgyro.nay, sqrt(pow(accelgyro.nax, 2) + pow(accelgyro.naz, 2))) * 180) / 3.14;
  angleY = - angleY;


  // Yaw Angle based on acelerometer
  //angleZ = accelGyroRelation * (angleZ + accelgyro.ngz * (float(dT) / 1000000)) + (1 - accelGyroRelation) *
  //         (atan2(sqrt(pow(accelgyro.nax, 2) + pow(accelgyro.nay, 2)), accelgyro.naz) * 180) / 3.14;

  //  mxCalibrated = my - ((myMax + myMin) / 2.0);
  //  myCalibrated = mx - ((mxMax + mxMin) / 2.0);
  //  mzCalibrated = mz - ((mzMax + mzMin) / 2.0);
  //
  //  angleZ = atan2( (mzCalibrated * sin(angleX) - myCalibrated * cos(angleX)),
  //                  (mxCalibrated * cos(angleY) + myCalibrated * sin(angleY) * sin(angleX) + mzCalibrated * sin(angleY) * cos(angleX))  ) * (180 / 3.14);

  // Yaw Angle Based on Compass
  compassCalculation();
  angleZ = mediaMovel(reads);
}


/* To calculate heading in degrees. 0 degree indicates North
   Calculate in radians
   xC = mx - ((mxMax + mxMin) / 2.0);
   yC = my - ((myMax + myMin) / 2.0);
   zC = mz - ((mzMax + mzMin) / 2.0);
*/
void compassCalculation() { //256us
  //calculation
  //Soft Iron and Hard Iron alibration
  float Sx = (float(myMax) - float(myMin))/(float(mxMax) - float(mxMin));
  float Sy = (float(mxMax) - float(mxMin))/(float(myMax) - float(myMin));

  if(Sx<1){
    Sx = 1;
  }
  if(Sy<1){
    Sy = 1;
  }
  
  float Ox = (float(mxMax - mxMin) / 2.0 - float(mxMax)) * Sx;
  float Oy = (float(myMax - myMin) / 2.0 - float(myMax)) * Sy;
  
//  Just Hard Iron
//  float Sx = 1;
//  float Sy = 1;
//  float Ox = float(mxMax + mxMin) / 2.0;
//  float Oy = float(myMax + myMin) / 2.0;
  compassAngle = atan2(Sy * (my + Oy), Sx * ( mx + Ox)) * (180 / PI);
  compassAngle = compassAngle - 180;


  Serial.print("\tSx: "); Serial.print(Sx);
  Serial.print("\tSy: "); Serial.print(Sy);
  Serial.print("\tOx: "); Serial.print(Ox);
  Serial.print("\tOy: "); Serial.println(Oy);
  
  //check if it north
  if (compassAngle >= 360) {
    compassAngle -= 360;
  }
  if (compassAngle < 0) {
    compassAngle += 360;
  }

  //pass it for an array to stabilizate the data
  for (int i = 0; i < mediaMovelArray - 1; i++) {
    reads[i] = reads[i + 1];
  }
  reads[mediaMovelArray - 1] = compassAngle;

}

/*
   Calculate the media of an array
*/
float mediaMovel(float *vetor) {
  float soma = 0;
  for (int i = 0; i < mediaMovelArray; i++) {
    soma += vetor[i];
  }
  return soma / mediaMovelArray;
}


void compassCalibration() {
  mxMax = 0;
  mxMin = 0;
  myMax = 0;
  myMin = 0;
  mzMax = 0;
  mzMin = 0;

  long unsigned int t_cal = millis();
  while ((millis() - t_cal) < (CALIBRATING_TIME * 1000)) {
    wdt_reset();
    if (bluetoothSerial.available() > 0) {
      bluetoothSerial.read(); //flush buffer11
      bluetoothSerial.print("c,c\n");
    }
    mag.getHeading(&mx, &my, &mz);
    if (mxMax < mx) {
      mxMax = mx;
    }
    if (mxMin > mx) {
      mxMin = mx;
    }
    if (myMax < my) {
      myMax = my;
    }
    if (myMin > my) {
      myMin = my;
    }
    if (mzMax < mz) {
      mzMax = mz;
    }
    if (mzMin > mz) {
      mzMin = mz;
    }

#ifdef DEBUG
    Serial.print("Calibrating! Time remaining (s):");
    Serial.println(CALIBRATING_TIME - (millis() - t_cal) / 1000);
#endif
    delay(10);
  }

  EEPROM.write(0, mxMin >> 8);  EEPROM.write(1, mxMin % 256);
  EEPROM.write(2, myMin >> 8);  EEPROM.write(3, myMin % 256);
  EEPROM.write(4, mzMin >> 8);  EEPROM.write(5, mzMin % 256);
  EEPROM.write(6, mxMax >> 8);  EEPROM.write(7, mxMax % 256);
  EEPROM.write(8, myMax >> 8);  EEPROM.write(9, myMax % 256);
  EEPROM.write(10, mzMax >> 8);  EEPROM.write(11, mzMax % 256);

#ifdef DEBUG
  printCalibrationInfo();
#endif
}

void ressetCalibration() {
  mxMax = 0;
  mxMin = 0;
  myMax = 0;
  myMin = 0;
  mzMax = 0;
  mzMin = 0;
  EEPROM.write(0, mxMin >> 8);  EEPROM.write(1, mxMin % 256);
  EEPROM.write(2, myMin >> 8);  EEPROM.write(3, myMin % 256);
  EEPROM.write(4, mzMin >> 8);  EEPROM.write(5, mzMin % 256);
  EEPROM.write(6, mxMax >> 8);  EEPROM.write(7, mxMax % 256);
  EEPROM.write(8, myMax >> 8);  EEPROM.write(9, myMax % 256);
  EEPROM.write(10, mzMax >> 8);  EEPROM.write(11, mzMax % 256);
}

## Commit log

2020-11-15 Estágios Iniciais
    Relatório Inicial, programas teste e CAD
    [Ball Head.SLDASM, Ball Head.STEP, Druckstück.sldprt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]
2020-11-16 NPF e Relatório
    [NPF Rule for sharp stars.xlsx]
2020-11-20 CAD update
    [BDT_GLOBAL_ASSEMBLY.SLDASM, BDT_G_F_05_v01.sldprt, BDT_G_F_09_v01.SLDPRT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]
2020-12-07 Electronic Circuit rev 1
2021-01-03 update 02-01
    [BDT_GLOBAL_ASSEMBLY.SLDASM, BDT_G_F_05_v01.sldprt, BDT_G_F_09_v01.SLDPRT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]
2021-01-24 complementary filter
    [configuration.h]
2021-02-08 filenames correction
    [BDT_E_P_01_v01.SLDPRT, BDT_E_P_02_v01.SLDPRT, BDT_E_P_03_v01.SLDPRT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]
2021-02-19 Fabricação
    [BDT_E_P_03_v01.DWG, BDT_E_P_03_v01.SLDPRT, BDT_I_A_16_v01.SLDASM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]
2021-02-26 BDT_G_F_05_v01 Fabricação
    [BDT_G_F_05_v01.SLDDRW, BDT_G_F_05_v01.sldprt, BDT_I_A_16_v01.SLDASM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]
2021-04-11 stepper speed
    [configuration.h]
2021-04-17 Arduino Scripts
    [configuration.h]
2021-04-20 Speed Test 1
    [configuration.h]
2021-05-06 added bt protocol
    [configuration.h]
2021-05-11 Codeless with optmization
    [configuration.h]
2021-05-19 PCB revision and Arduino code clean
    [configuration.h]
2021-06-04 bugs and signal of angles fixed
    [bluetooth.ino, debug.ino, main.ino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]
2021-06-14 sketch correction
    [BDT_I_A_16_v01.SLDASM, BDT_I_P_06_v01.sldprt, BDT_I_P_07_v01.sldprt]
2021-06-22 speed corrected and can accept double values
    [configuration.h]
2021-07-01 update codes at tcc and send for revision IHC
    [BDT_G_F_05_v01.sldprt, BDT_G_P_14_v01.sldprt, BDT_I_A_16_v01.SLDASM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]
2021-07-13 Atualização CAD
    [BDT_I_A_16_v01.SLDASM, BDT_S_A_17_v01.SLDASM, arruela.SLDPRT]
2021-07-16 secao 2.1
    [BDT_I_A_16_v01.SLDASM, BDT_S_A_17_v01.SLDASM]
2021-11-23 rev 4 belts
2022-05-23 gitignore update
    [BDT_E_P_03_v01.SLDPRT]

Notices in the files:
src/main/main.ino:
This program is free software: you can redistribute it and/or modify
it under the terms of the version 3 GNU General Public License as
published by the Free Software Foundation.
